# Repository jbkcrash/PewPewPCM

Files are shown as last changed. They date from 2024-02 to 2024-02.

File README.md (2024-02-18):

# PewPewPWM
PWM Laser Controller for Synrad 48-1KAM and other compatible lasers.

This project uses a PI Pico, it's support for PWM, and a simple circuit used to shift level and buffer the output.

We use a couple AND gates, a 2N3904 Transistor, a couple resistors and capacitors for filtering, to level shift a PWM output from the PI Pico, generating the 5Khz/1uS Tickle pulses and integrated PWM signal to control the laser power. The Tickle is always maintained at no PWM for Laser output stability and hardware durability.

Currently it only supports a simple Text-based serial interface with no real safety disable. The vision for future is to create a simple Windows WPF application for an additional GUI interface, support on-time duration settings(Pulse-On Modes), and add a normally closed safety kill switch.

As of the end of winter '24 this is my primary hobby project, so check back for more details and videos!

## Schematics
[Circuit Used](Circuit/circuit.png)

Initial BOM:
- 1ea 2N3904
- 1ea 220 Ohm
- 1ea 1K Ohm
- 1ea 10uF 50V Electrolytic
- 1ea 100nF
- 1ea SN7408N, about any two TTL __AND__ or other Gates, including Buffers would work
Note - If you use different gates remember to adapt the circuit when using negated logic.
- 1ea BNC connector
- 1ea PI PICO or equivilant MicroPython(For included software to work) MCU

I also added a couple signal Diodes for simple circuit protection and noise filter. These are optional.
- 2ea 1N4148

## Case STLs
3D Printable Files
Top:
[Case Top](STL/PewPewPWM_Top.stl)
Case:
[Case](STL/PewPewPWM_Case.stl)

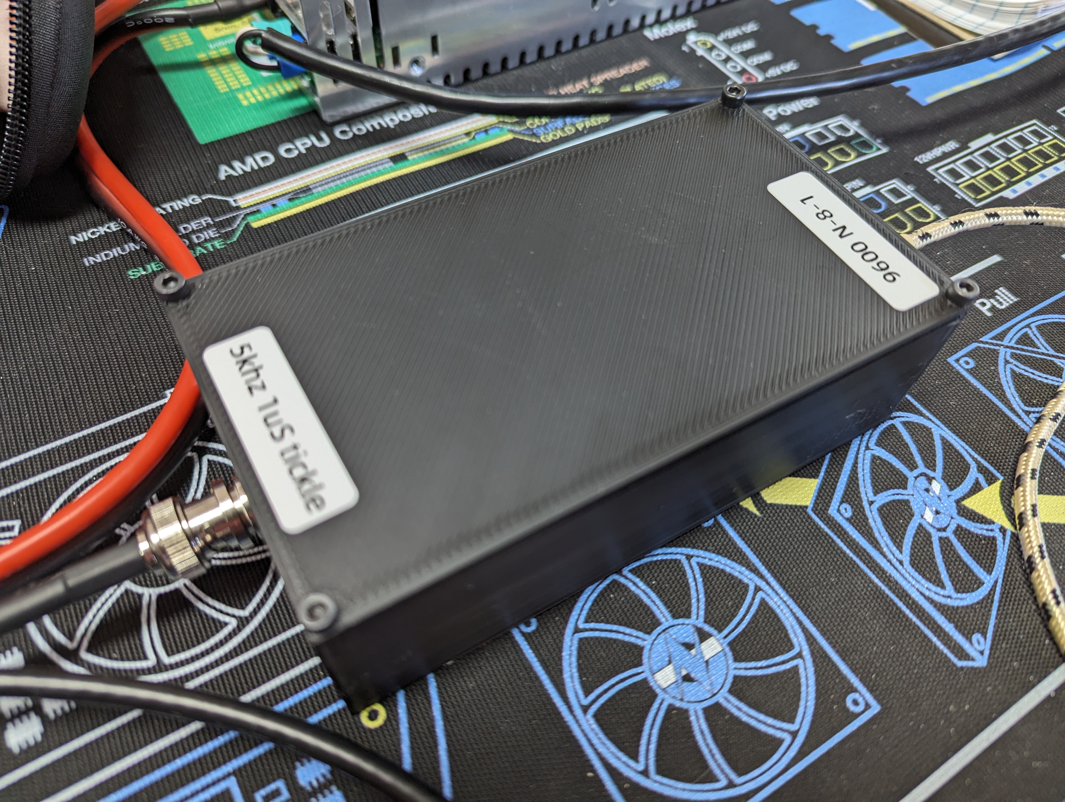
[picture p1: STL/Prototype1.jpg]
Image of case

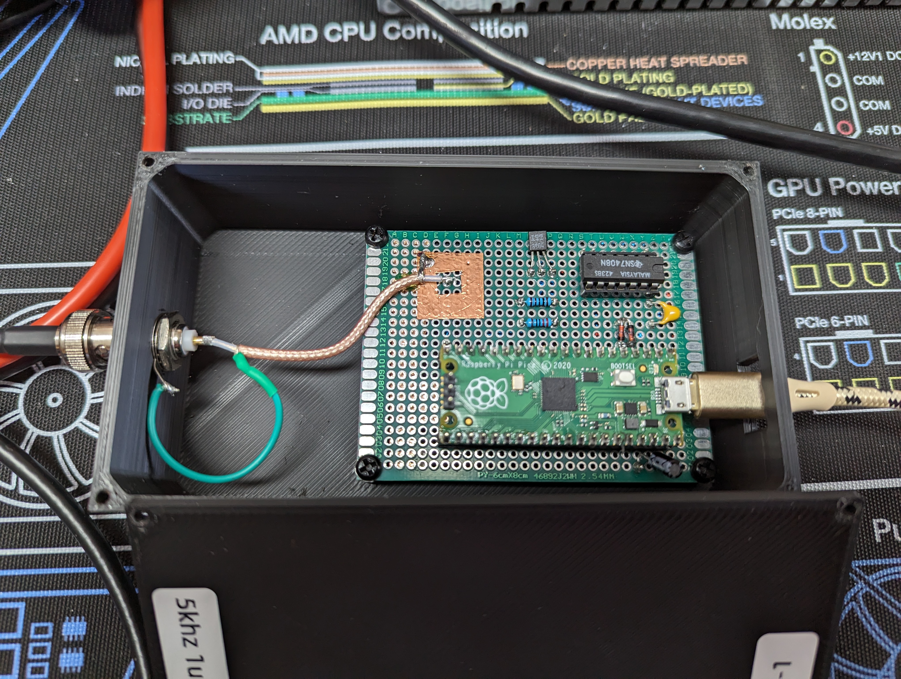
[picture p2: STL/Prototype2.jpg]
Image of Protoboad w/Circuit


## Short video of my laser in operation
Short Video of Focused Laser (https://www.youtube.com/shorts/cXQKUah9bkY)

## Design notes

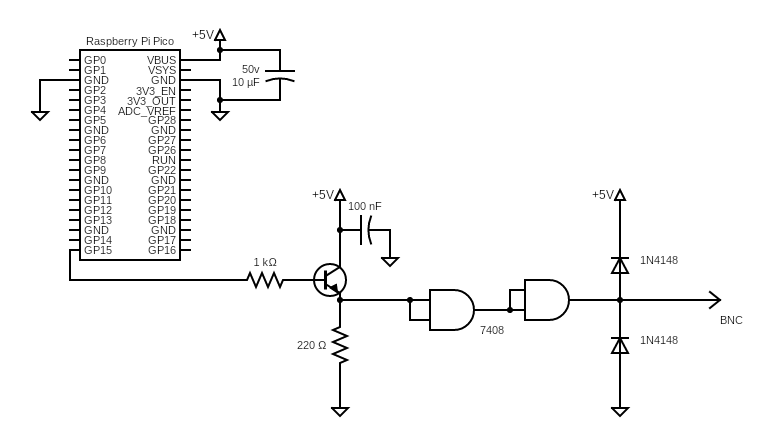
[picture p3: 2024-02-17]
Circuit/circuit.png

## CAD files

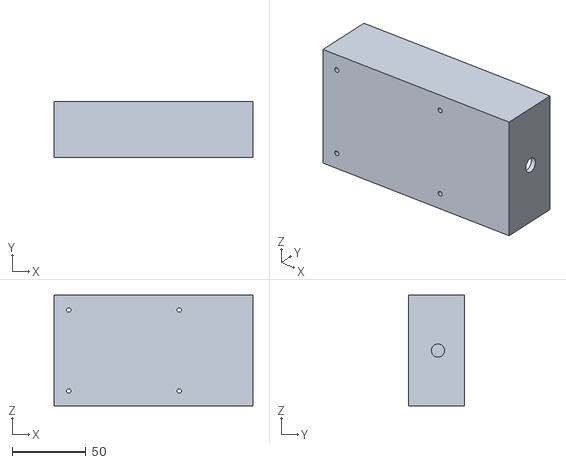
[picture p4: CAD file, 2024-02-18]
STL/PewPewPWM_Case.stl
135.0 x 38.0 x 75.0

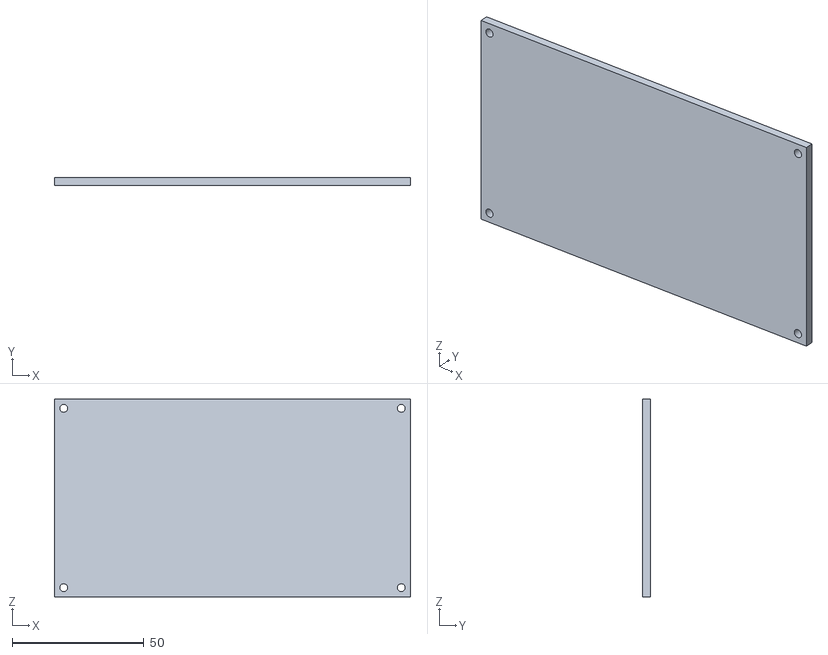
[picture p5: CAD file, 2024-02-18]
STL/PewPewPWM_Top.stl
135.0 x 3.00 x 75.0

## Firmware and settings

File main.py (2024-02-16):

from machine import Pin, PWM
from time import sleep

# Setup the PWM for CO2 Laser
# For 48-1KAM we need a constant 1us Tickle. Then the duty defines power from there.
pwm = PWM(Pin(15))

freq=5000
tickle_ns=1000 #.5% is the tickle preionization PWM percentage
pwm.init(freq=freq, duty_ns=tickle_ns)

def get_ns(percent): # Function to convert percentage return corresponding nanosecond value.
    if not 0 < percent <= 100:
        return tickle_ns
    tickle_duty = percent*2000  # Convert percentage input into desired nanosecond value within the calculated period range by scaling it with respect to maximum possible duty cycle which is equal half of total time duration or one complete pulse width (5µs in this case).
    return tickle_duty   # Return corresponding nanosecond equivalent as output

sleep(2) #Give us time to get on serial...

print("It is safe to power on the laser!")

while True:
    try:
        percent = input("Enter Power Level in percent, or \"off\": ")
    except:
        sleep(5)
        continue
    if percent=="off" or percent == "Off":
        pwm.duty_ns(tickle_ns)
        print("Laser is in tickle precharge mode, it is safe to power off.")
        continue
    try:
        percent = int(float(percent))
        pwm.duty_ns(get_ns(percent))
    except:
        print("You must enter an integer percentage between 1 and 100")
        pwm.duty_ns(tickle_ns) # Rather than leave the laser on, lets turn it off to be safe!    
    
    #for duty in range(65025):
    #    pwm.duty_u16(duty)
    #    sleep(0.0001)
    #for duty in range(65025, 0, -1):
    #    pwm.duty_u16(duty)
    #    sleep(0.0001)

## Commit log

2024-02-17 Adding Circuit
2024-02-18 Added Case STL
    [PewPewPWM_Case.stl, PewPewPWM_Top.stl]
2024-02-18 Adding diodes and fixing README
